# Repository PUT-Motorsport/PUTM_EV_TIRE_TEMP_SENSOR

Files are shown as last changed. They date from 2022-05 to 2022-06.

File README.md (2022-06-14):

# Tire Temperature Sensor
This is the STM32 board which sends the data collected from the IR Sensor through the CAN bus.
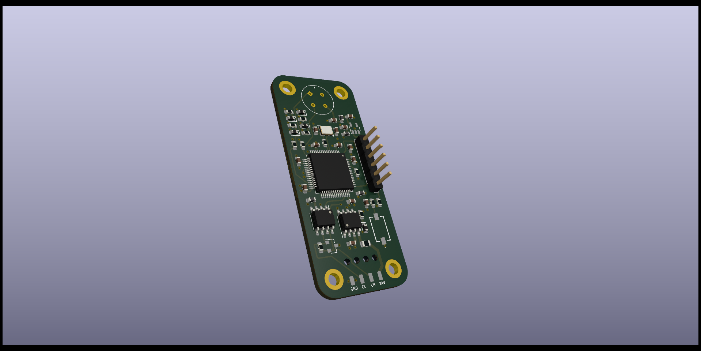
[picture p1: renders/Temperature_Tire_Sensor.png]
front

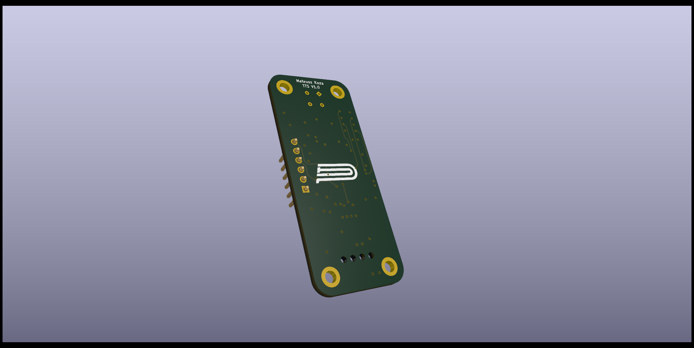
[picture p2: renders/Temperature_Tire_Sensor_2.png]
back


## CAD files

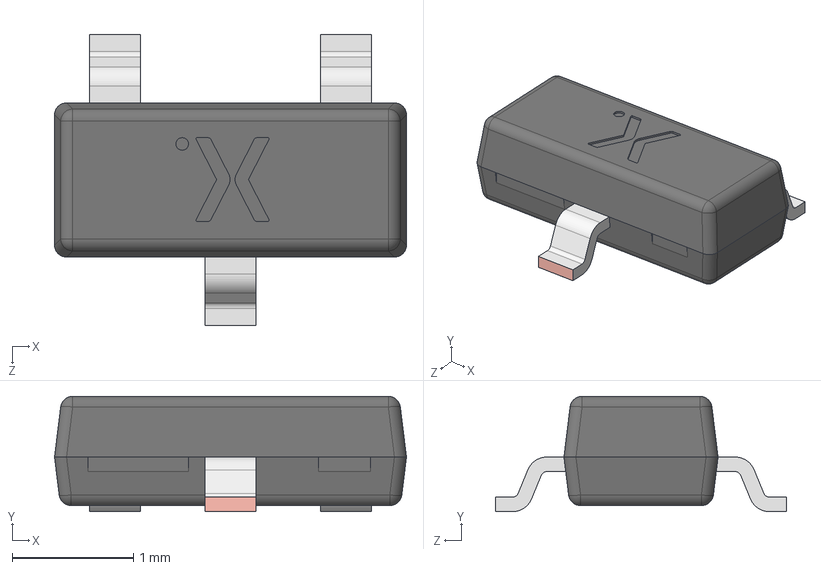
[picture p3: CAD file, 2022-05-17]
HARDWARE/Temperature_Tire_Sensor/LIB_PESD2CAN,215/PESD2CAN,215/3D/PESD2CAN,215.stp
2.90 x 0.95 x 2.40 mm
SOT23 lower body
SOT23 Lead x 3
SOT23 Upper body

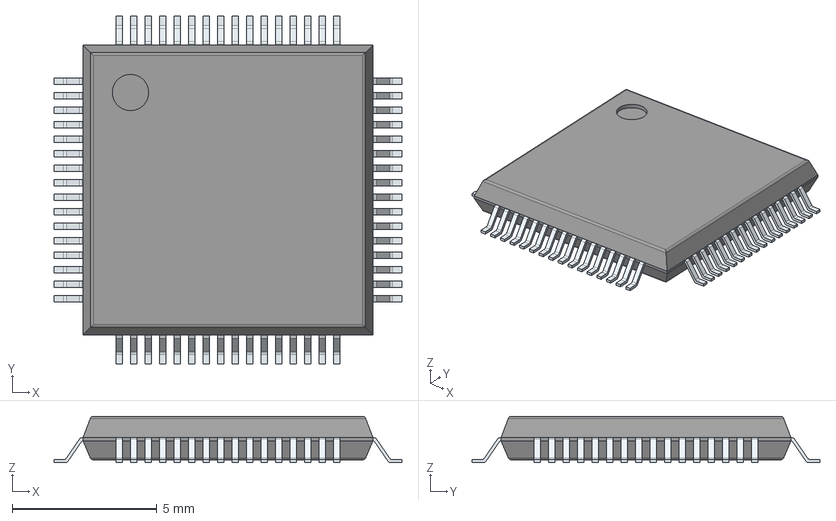
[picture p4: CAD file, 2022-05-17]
HARDWARE/Temperature_Tire_Sensor/LIB_STM32L4P5RET6/STM32L4P5RET6/3D/STM32L4P5RET6.stp
12.0 x 12.0 x 1.60 mm
PinsArrayLR
PinsArrayTB

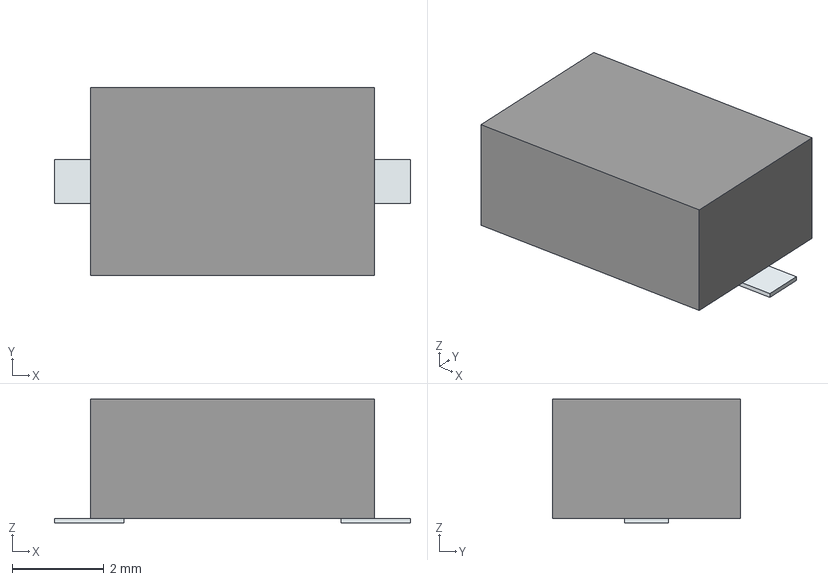
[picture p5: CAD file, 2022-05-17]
HARDWARE/Temperature_Tire_Sensor/434781025816/3D/434781025816.stp
7.76 x 4.10 x 2.70 mm
Pins

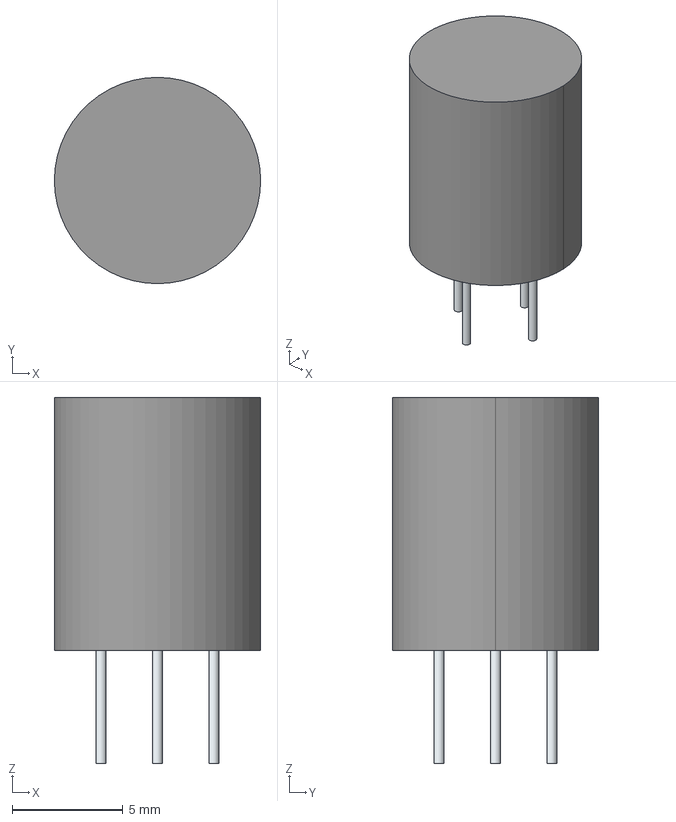
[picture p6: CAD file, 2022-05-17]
HARDWARE/Temperature_Tire_Sensor/LIB_MLX90621ESF-BAB-000-SP/MLX90621ESF-BAB-000-SP/3D/MLX90621ESF-BAB-000-SP.stp
9.30 x 9.30 x 16.5 mm
Leads x 4

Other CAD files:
HARDWARE/Temperature_Tire_Sensor/434781025816/3D/434781025816.stl
HARDWARE/Temperature_Tire_Sensor/434781025816/Allegro/434781025816.psm
HARDWARE/Temperature_Tire_Sensor/434781025816/DEHDL/434781025816/chips/chips.prt
HARDWARE/Temperature_Tire_Sensor/LIB_MLX90621ESF-BAB-000-SP/MLX90621ESF-BAB-000-SP/3D/MLX90621ESF-BAB-000-SP.stl
HARDWARE/Temperature_Tire_Sensor/LIB_MLX90621ESF-BAB-000-SP/MLX90621ESF-BAB-000-SP/Allegro/mlx90621esfbab000sp.psm
HARDWARE/Temperature_Tire_Sensor/LIB_MLX90621ESF-BAB-000-SP/MLX90621ESF-BAB-000-SP/DEHDL/mlx90621esf_bab_000_sp/chips/chips.prt
HARDWARE/Temperature_Tire_Sensor/LIB_NCV8775CDT33RKG/NCV8775CDT33RKG/Allegro/ncv8775cdt33rkg.psm
HARDWARE/Temperature_Tire_Sensor/LIB_NCV8775CDT33RKG/NCV8775CDT33RKG/DEHDL/ncv8775cdt33rkg/chips/chips.prt
HARDWARE/Temperature_Tire_Sensor/LIB_PESD2CAN,215/PESD2CAN,215/Allegro/sot95p230x110-3n.psm
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

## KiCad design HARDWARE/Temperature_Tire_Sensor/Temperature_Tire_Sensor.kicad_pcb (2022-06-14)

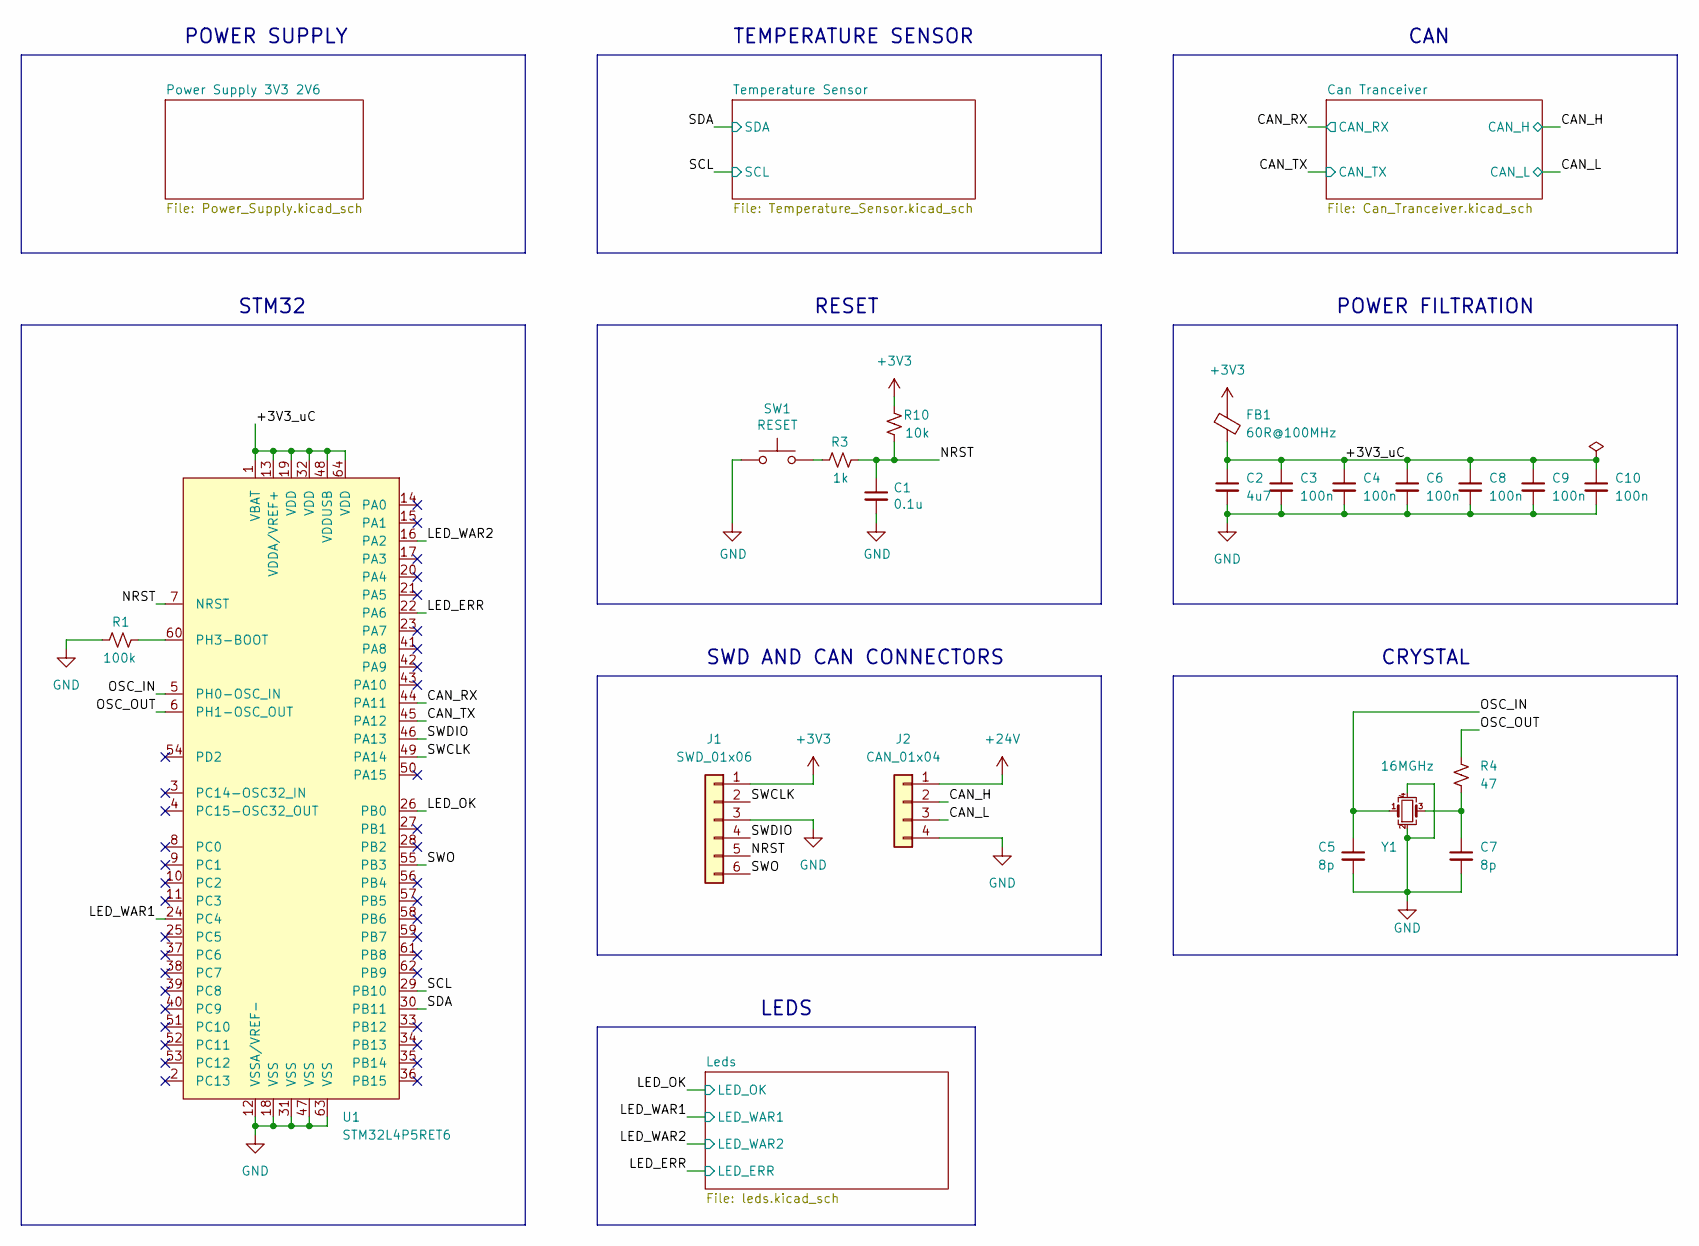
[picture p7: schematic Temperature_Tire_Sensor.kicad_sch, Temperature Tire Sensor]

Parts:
C1: 0.1u; C_0603_1608Metric
C2: 4u7; C_0603_1608Metric
C3, C4, C6, C8, C9, C10: 100n; C_0603_1608Metric
C5, C7: 8p; C_0603_1608Metric
FB1: 60R@100MHz; L_0603_1608Metric
J1: SWD_01x06; PinHeader_1x06_P2.54mm_Vertical
J2: CAN_01x04; SolderWirePad_1x04_SMD_1x2mm
R1: 100k; R_0603_1608Metric
R3: 1k; R_0603_1608Metric
R4: 47; R_0603_1608Metric
R10: 10k; R_0603_1608Metric
SW1: RESET; 434781025816
U1: STM32L4P5RET6; LQFP-64_10x10mm_P0.5mm
Y1: 16MGHz; Crystal_SMD_SeikoEpson_TSX3225-4Pin_3.2x2.5mm

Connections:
+3V3: FB1.1, J1.1, R10.2; also elsewhere on the board
+24V: J2.1; also elsewhere on the board
/+3V3_uC: C2.1, C3.1, C4.1, C6.1, C8.1, C9.1, C10.1, FB1.2, U1.1 (VBAT), U1.13 (VDDA/VREF+), U1.19 (VDD), U1.32 (VDD), U1.48 (VDDUSB), U1.64 (VDD)
/CAN_H: J2.2; also elsewhere on the board
/CAN_L: J2.3; also elsewhere on the board
/CAN_RX: U1.44 (PA11); also elsewhere on the board
/CAN_TX: U1.45 (PA12); also elsewhere on the board
/LED_ERR: U1.22 (PA6); also elsewhere on the board
/LED_OK: U1.26 (PB0); also elsewhere on the board
/LED_WAR1: U1.24 (PC4); also elsewhere on the board
/LED_WAR2: U1.16 (PA2); also elsewhere on the board
/NRST: C1.1, J1.5, R3.2, R10.1, U1.7 (NRST)
/OSC_IN: C5.1, U1.5 (PH0-OSC_IN), Y1.1
/OSC_OUT: R4.1, U1.6 (PH1-OSC_OUT)
/SCL: U1.29 (PB10); also elsewhere on the board
/SDA: U1.30 (PB11); also elsewhere on the board
/SWCLK: J1.2, U1.49 (PA14)
/SWDIO: J1.4, U1.46 (PA13)
/SWO: J1.6, U1.55 (PB3)
GND: C1.2, C2.2, C3.2, C4.2, C5.2, C6.2, C7.2, C8.2, C9.2, C10.2, J1.3, J2.4, R1.2, SW1.1, U1.12 (VSSA/VREF-), U1.18 (VSS), U1.31 (VSS), U1.47 (VSS), U1.63 (VSS), Y1.2, Y1.4; also elsewhere on the board
unnamed: C7.1, R4.2, Y1.3
unnamed: R1.1, U1.60 (PH3-BOOT)
unnamed: R3.1, SW1.2

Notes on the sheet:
CAN
CRYSTAL
SWD AND CAN CONNECTORS
TEMPERATURE SENSOR
LEDS
RESET
STM32
POWER FILTRATION
POWER SUPPLY

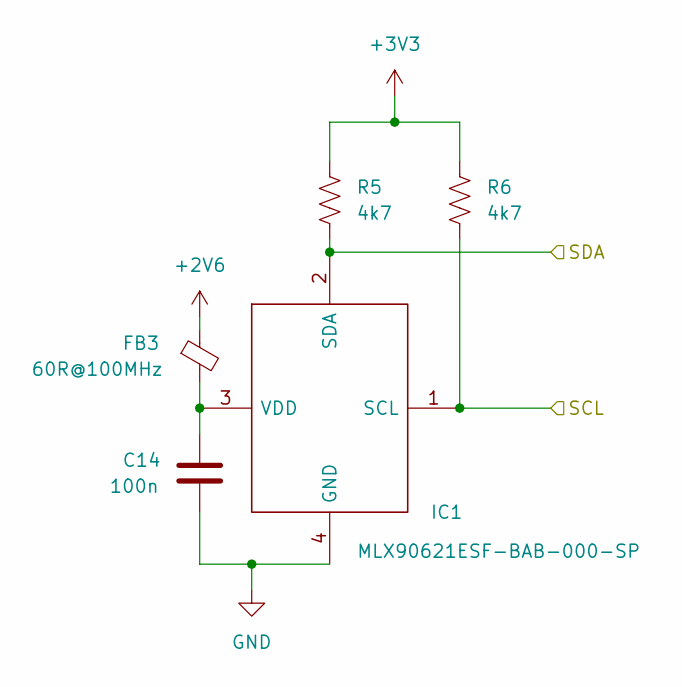
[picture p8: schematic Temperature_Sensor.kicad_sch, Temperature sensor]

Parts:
C14: 100n; C_0603_1608Metric
FB3: 60R@100MHz; L_0603_1608Metric
IC1: MLX90621ESF-BAB-000-SP; MLX90621ESFBAB000SP; Manufacturer_Part_Number MLX90621ESF-BAB-000-SP; Mouser Part Number 482-90621ESFBAB000SP
R5, R6: 4k7; R_0603_1608Metric

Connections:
+2V6: FB3.1; also elsewhere on the board
+3V3: R5.1, R6.1; also elsewhere on the board
/SCL: IC1.1 (SCL), R6.2; also elsewhere on the board
/SDA: IC1.2 (SDA), R5.2; also elsewhere on the board
GND: C14.2, IC1.4 (GND); also elsewhere on the board
unnamed: C14.1, FB3.2, IC1.3 (VDD)

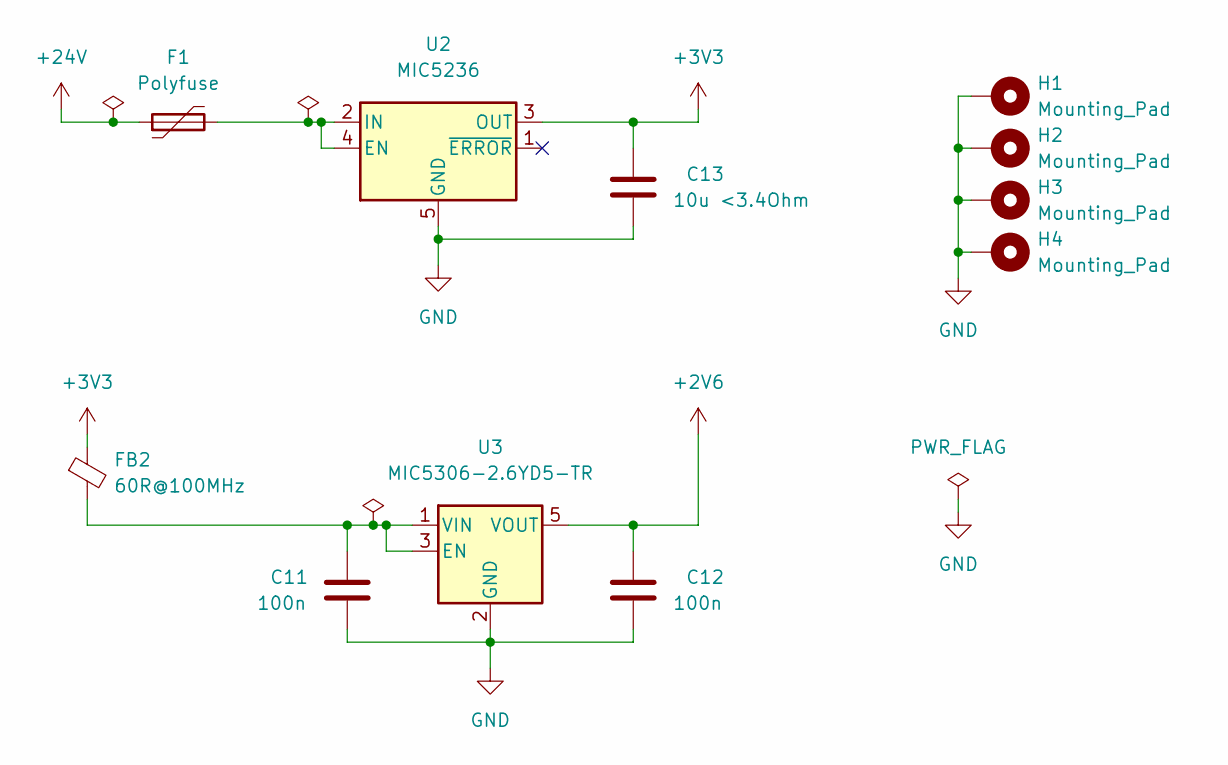
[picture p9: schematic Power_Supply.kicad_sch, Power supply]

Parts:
C11, C12: 100n; C_0603_1608Metric
C13: 10u <3.4Ohm; C_0603_1608Metric
F1: Polyfuse; Fuse_0805_2012Metric
FB2: 60R@100MHz; L_0603_1608Metric
H1, H2, H3, H4: Mounting_Pad; MountingHole_2.7mm_M2.5_ISO14580_Pad
U2: MIC5236; SOIC-8_3.9x4.9mm_P1.27mm
U3: MIC5306-2.6YD5-TR; TSOT-23-5

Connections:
+2V6: C12.1, U3.5 (VOUT); also elsewhere on the board
+3V3: C13.1, FB2.1, U2.3 (OUT); also elsewhere on the board
+24V: F1.1; also elsewhere on the board
GND: C11.2, C12.2, C13.2, H1.1, H2.1, H3.1, H4.1, U2.5 (GND), U2.6 (GND), U2.7 (GND), U2.8 (GND), U3.2 (GND); also elsewhere on the board
unnamed: C11.1, FB2.2, U3.1 (VIN), U3.3 (EN)
unnamed: F1.2, U2.2 (IN), U2.4 (EN)

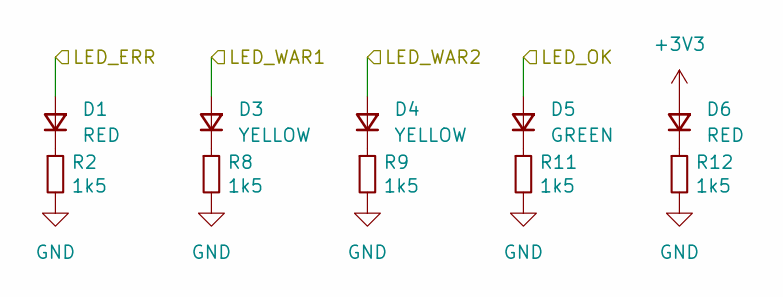
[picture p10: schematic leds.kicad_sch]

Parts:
D1, D6: RED; D_0603_1608Metric
D3, D4: YELLOW; D_0603_1608Metric
D5: GREEN; D_0603_1608Metric
R2, R8, R9, R11, R12: 1k5; R_0603_1608Metric

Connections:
+3V3: D6.2 (A); also elsewhere on the board
/LED_ERR: D1.2 (A); also elsewhere on the board
/LED_OK: D5.2 (A); also elsewhere on the board
/LED_WAR1: D3.2 (A); also elsewhere on the board
/LED_WAR2: D4.2 (A); also elsewhere on the board
GND: R2.2, R8.2, R9.2, R11.2, R12.2; also elsewhere on the board
unnamed: D1.1 (K), R2.1
unnamed: D3.1 (K), R8.1
unnamed: D4.1 (K), R9.1
unnamed: D5.1 (K), R11.1
unnamed: D6.1 (K), R12.1

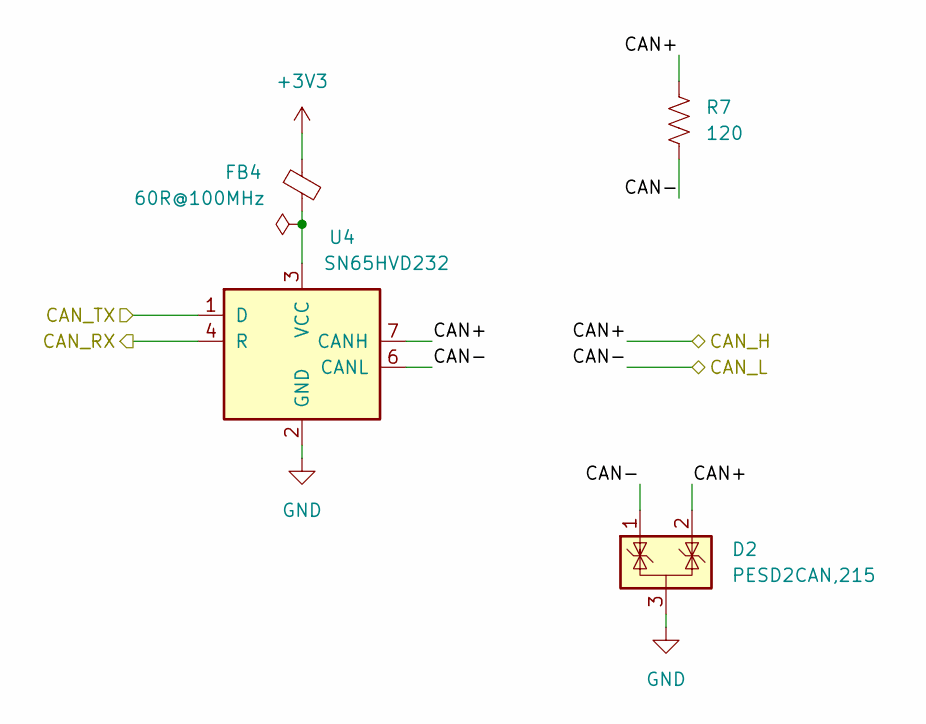
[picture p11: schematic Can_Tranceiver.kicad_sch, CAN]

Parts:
D2: PESD2CAN,215; SOT-23
FB4: 60R@100MHz; L_0603_1608Metric
R7: 120; R_0603_1608Metric
U4: SN65HVD232; SOIC-8_3.9x4.9mm_P1.27mm

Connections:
+3V3: FB4.1; also elsewhere on the board
/CAN_H: D2.2 (K), R7.1, U4.7 (CANH); also elsewhere on the board
/CAN_L: D2.1 (K), R7.2, U4.6 (CANL); also elsewhere on the board
/CAN_RX: U4.4 (R); also elsewhere on the board
/CAN_TX: U4.1 (D); also elsewhere on the board
GND: D2.3 (A), U4.2 (GND); also elsewhere on the board
unnamed: FB4.2, U4.3 (VCC)

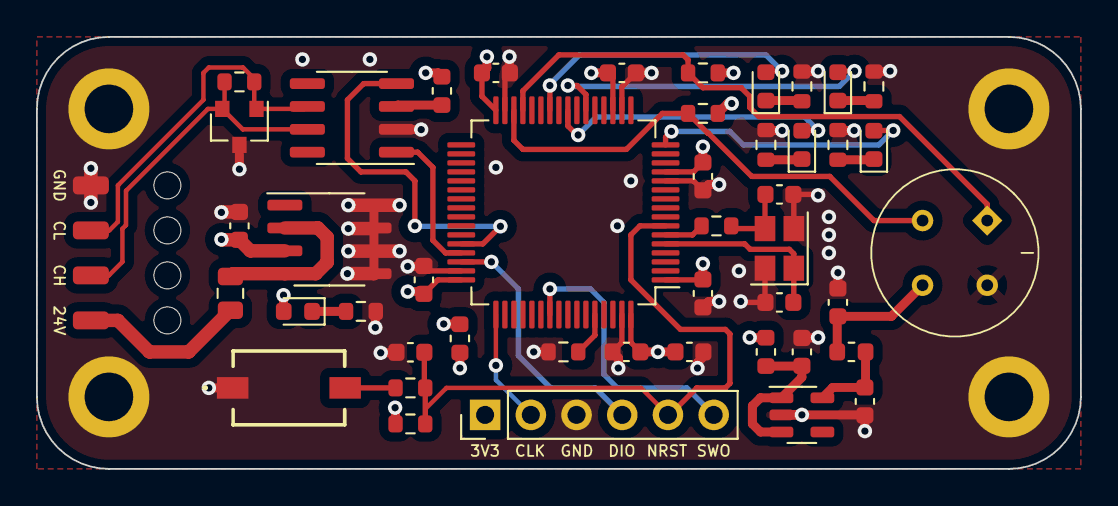
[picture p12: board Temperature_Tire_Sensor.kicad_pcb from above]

Board: 4 copper layers, 58.0 x 24.0 mm, 50 parts (0 on the bottom side), 33 nets.

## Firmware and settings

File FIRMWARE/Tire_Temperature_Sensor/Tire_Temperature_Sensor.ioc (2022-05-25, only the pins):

Mcu.UserName=STM32L4P5RETx
PA11.Signal=CAN1_RX
PA12.Signal=CAN1_TX
PA2.GPIO_Label=LED_WAR2
PA2.Signal=GPIO_Output
PA6.GPIO_Label=LED_ERR
PA6.Signal=GPIO_Output
PB0.GPIO_Label=LED_OK
PB0.Signal=GPIO_Output
PB10.Signal=I2C2_SCL
PB11.Signal=I2C2_SDA
PC4.GPIO_Label=LED_WAR1
PC4.Signal=GPIO_Output

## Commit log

2022-05-17 pcb layout nearly completed
    [434781025816.psm, 434781025816.stl, 434781025816.stp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]
2022-05-18 pcb layout is done/has to be checked
    [Power_Supply.kicad_sch, Temperature_Tire_Sensor.kicad_pcb, Temperature_Tire_Sensor.kicad_sch]
2022-05-25 Routing is done - has to be checked
    [Can_Tranceiver.kicad_sch, Power_Supply.kicad_sch, Temperature_Sensor.kicad_sch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]
2022-05-26 TTS V1.0 - needs to be checked
    [Temperature_Tire_Sensor.kicad_pcb]
2022-06-13 Preproduction review.
    [Temperature_Tire_Sensor.kicad_pcb, Temperature_Tire_Sensor.kicad_sch]
2022-06-14 Silkscreen layout has been changed
    [Temperature_Tire_Sensor.kicad_pcb]
